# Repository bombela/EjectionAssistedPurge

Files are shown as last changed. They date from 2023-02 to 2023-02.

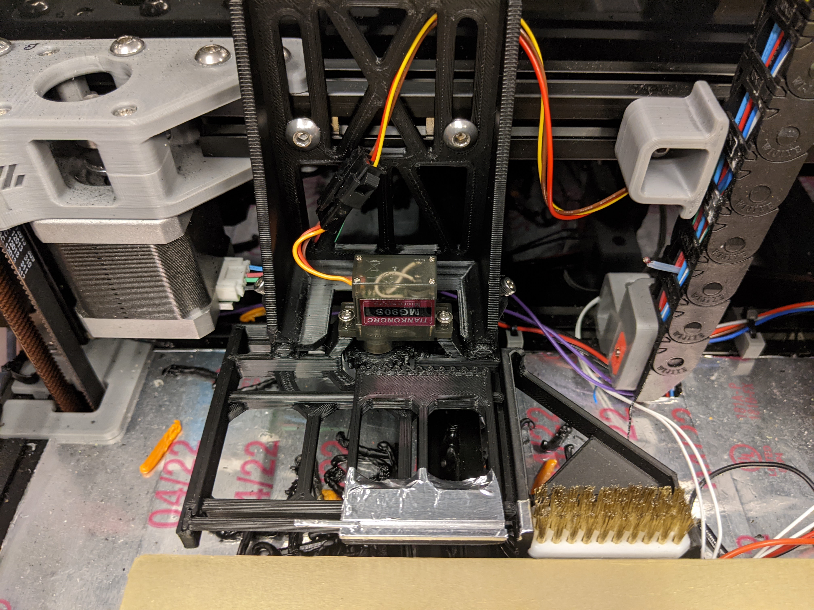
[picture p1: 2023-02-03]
doc/installed_closeup.jpg

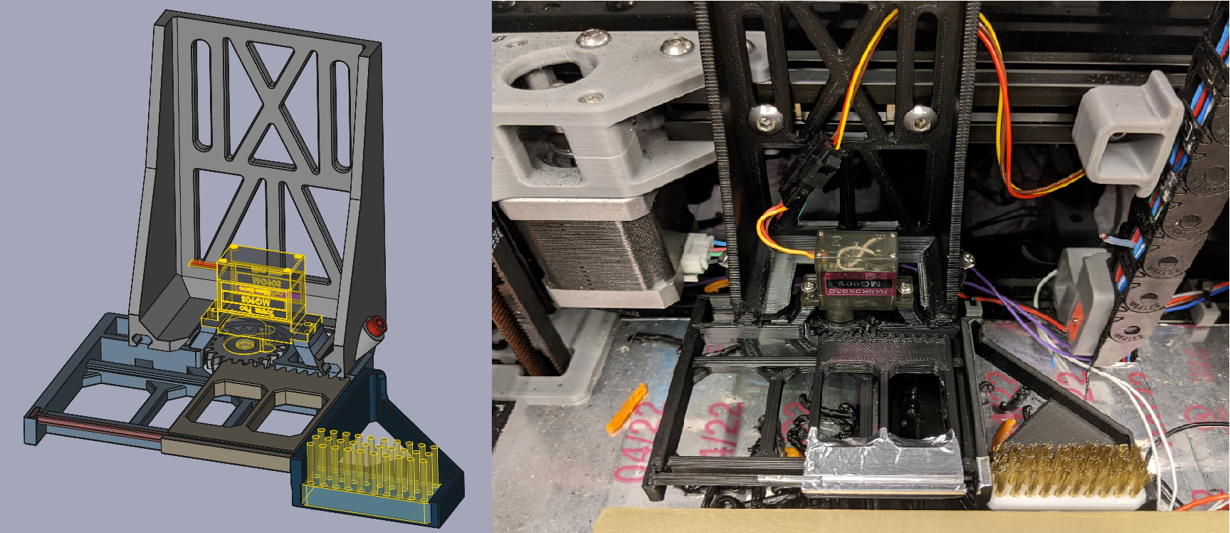
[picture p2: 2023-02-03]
doc/overview.png

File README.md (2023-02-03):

# EjectionAssistedPurge (EAP)

https://user-images.githubusercontent.com/216204/216499002-51c40538-1833-44a0-8337-d1b87039a244.mp4

Designed for the Voron 2.4r2. Should work on Voron Trident. Feel free modify it for other printers.
There are macros for Klipper to brush, purge, and integrate with the slicer toolchange.

The EAP can purge from 15mm³ to 185mm³. For reference, the default purge amount in PrusaSlicer and SuperSlicer is 140mm³.

It is especially useful with an automatic filament changer, like the [ERCF](https://github.com/EtteGit/EnragedRabbitProject).

# Overview

overview

The EAP mounts on the gantry of a Voron 2.4 (or the frame for a Trident). Therefore it is always at the same Z height as the nozzle.
It is adjustable in Z and Y. Purging is done into a groove with a dovetail shape designed to hold the hot plastic, and resist curl up.
The groove is covered with adhesive metallic foil to quickly cool the surface of the extrusion and prevent adhesion.

The plastic should be left to cool from 15s (ABS) to 30s (95A TPU) before ejection.
In practice, automatic filament changes takes about 30s, so even printing a single dot between swaps gives it enough time to cool.

The Grove is 1mm from the edge of the tray, and 2mm wide. This means that the tray can be as close as possible to the bed,
and only a couple milimeters past the back end of the bed. With the stock Voron 2.4r2 nothing has to be adjusted.
It is similar to reaching out to the nozzle endstop.

An ubiquitous RC Servo MG90S is used to actuate the tray against a piston and eject the solidifed plastic. There is no provision
to catch the plastic turds. They accumulate at the bottom of the printer, and this can be cleaned up from time to time.

It has been tested succesfully with ABS, PLA, PETG and 95A TPU.

# Printing, BOM, and assembly

parts laid out for printing

All the [STL/STEP files](/stl) files are oriented for printing. The screenshot above shows all the parts spread out.

The design is optimized for ABS and accounts for shrinkage. I slice with arachnea, 0.2mm layer height, 0.4mm nozzle, 4 perimeters, 5 layers bottom/top, and 15% gyroid infill. Standard Voron recommended settings should also work fine.

## Bill of material

 - 2× (M5x8 + M5 tnut) for mounting the bracket on the gantry (and finely adjust in Z).
 - 2× M3x8 to lock the frame in  Y adjustment.
 - MG90S or similar RC servo 180° and the screws that come with it.
 - Aluminum adhesive tape: ~10µm thick, 20 to 40mm wide.
 - A brass brush, you know, the one we all use.
 
And for RC servo connection on the Octopus board:
 - 3×24 awg 150cm long
 - JST-XH 2pins male connector
 - JST-XH 3pins male connector
 - Optional, some wire-to-wire connector near the servo for conveniance.

## Assembly instructions

### Adhesive aluminum tape

The difficult part is the aluminum adhesive foil on the tray. Refer to the pictures for where to place the tape.

A trick is to fold it, insert it in the groove. Then gently spread it out with the shaft
of a thin screwdriver used in its whole length.
It is important for the foil to follow the contour of the grove tightly. Otherwise it will rip when the piston moves through.
Manually insert the piston and test. Redo the work if necessary, it took me 5 tries the first time.

You can extend the aluminum foil over the tray up to the rack teeth with another piece if necessary.
The large the surface area, the better the cooling.

Add a piece of adhesive aluminum tape at the tip of the piston. No need to cover the whole thing, nor the sides.
Just enough to cover the tip and prevent plastic from sticking. Finally, add one more small piece on the edge if the brush holder.
ABS tends to slide off the groove very easily and follow the nozzle. It could stick on the edge of the brush holder.

### Printed parts

Everything slides with dovetails. Install the tray first. The piston next. Slide the brush holder after that.
Insert the brush at the end, its easy to prick fingers otherwise.

Mount the pinion gear on the servo and the screw. Screw it quite tight. There is up to 1kg of force on the gear.
Then gently turn the gear into counter-clockwise (ie: as if unscrewing) until you reach the end of travel. Don't break the poor servo!

This way the gear is set for when the tray is all the way opened to the left. Place the tray all the way to the left,
the the servo. It is ok for the tray to not touch the frame when the gear engages. There is some margin on both sides.
Use the two M2 self-tapping screws that come with the servo to mount it on the frame.

Finally slide the frame into the bracket. Add the two M3 screws. Mount the bracket on the gantry. I choose to install
mine on the left side. And my [Klicky probe](https://github.com/jlas1/Klicky-Probe) on the right. I suppose you could
mirror the parts before printing. The Klipper macros are agnostic of the direction.

An easy way to install flush to the bed in Z and Y is to instruct the printer to move the toolhead to the far front and lower the nozzle on the bed.
Then the bracket can be mounted to the granty with the M5 screws and T-nut.
It is easy to adjust the Y and Z such that the top of the tray is flush with the top of the and side of the bed.
Do leave a minimum of 0.5mm from the edge of the bed. There a tiny bit of margin here, the nozzle doesn't have to be perfectly in the middle of the
grove, nor perfectly flush with the top surface of the tray.

The frame is locked in Y with the two M3 screws. No need to over-tighten there. It's threaded into plastic. 

The brush holder can be adjusted in Y independently by sliding the dovetail. For example if you want a larger gap from the bed and the tray,
you can move the brush forward a bit to get a better scrubbing of the nozzle.

### Electronics

You do need one available digital pin to control the servo. And a 5V supply.
With the Octopus board (stock Voron 2.4r2), I used PG12 on the DIAG4, and the fixed FAN7 output set for 5V.
This way, the wiring is tidy. You will need to crimp the JST connectors (listed in the BOM above).



Thread the wire through the Z drag chain. Follow the path of the nearest A/B motor wiring.

# Klipper macros

Include the `eap.cfg` in your Klipper configuration (most likely in `printer.cfg`).
Carefuly adjust the configuration variables at the top of the file.
Manually control your toolhead with Klipper to find out of the exact XY positions of the groove and the brush.

The macros and their parameters are documented in detail the file.

Ejection is done before purging. Maximizing the cooling time between purges.
This does wastes 2s before purging.
Klipper would need to be modified to support asyncronous actuation of the ejection.
I do not swap filament often, so for now this has not bothered me.

Here a summary of the macros:

|Macro|Description|
|-|-|
|BRUSH|Brush the nozzle. Useful in PRINT_START, PRINT_END, homing and Quand Gantry Leveling and so on.|
|PURGE|Eject, then purge and plow through the brush.|
|PURGE_HOME|Place the toolhead near the groove then eject. Used before a toolchange, see example of use in PrusaSlicer below.|
|PURGE_EJECT|Trigger an ejection. Useful for testing.|

## Use in PrusaSlicer

Here is an example of use in prusaslicer tool change gcode. When the wipe tower is turned off,
the Ejection Assisted Purge is used.

```
{if has_wipe_tower}
  T{next_extruder} ; ERCF swap { filament_preset[current_extruder] }
{else}
  PURGE_HOME ZHOP=0.2 ZCHECK=0
  T{next_extruder} ; ERCF swap { filament_preset[current_extruder] }
  PURGE VOL=150 RET=0.5 RETSPEED=35 EJECT=0 BRUSH_CLEAR=0 ZCHECK=0
{endif}
```

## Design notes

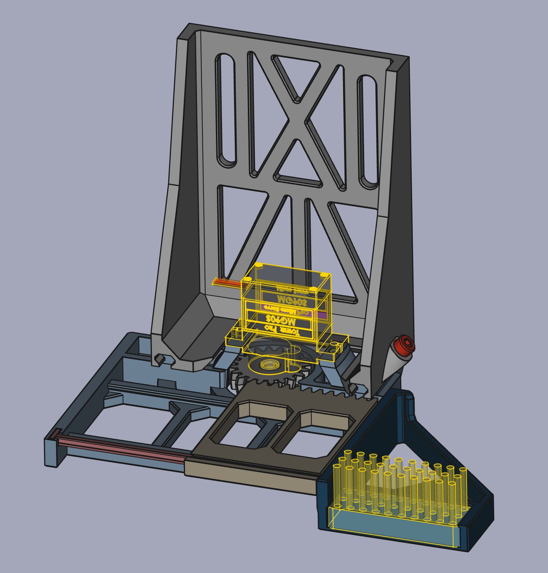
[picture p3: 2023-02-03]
doc/cad.jpg

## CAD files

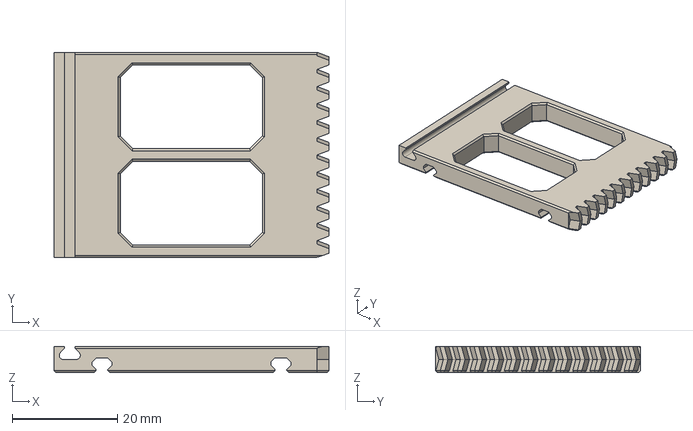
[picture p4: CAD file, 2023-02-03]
stl/eap_tray.step
52.2 x 39.0 x 5.00 mm

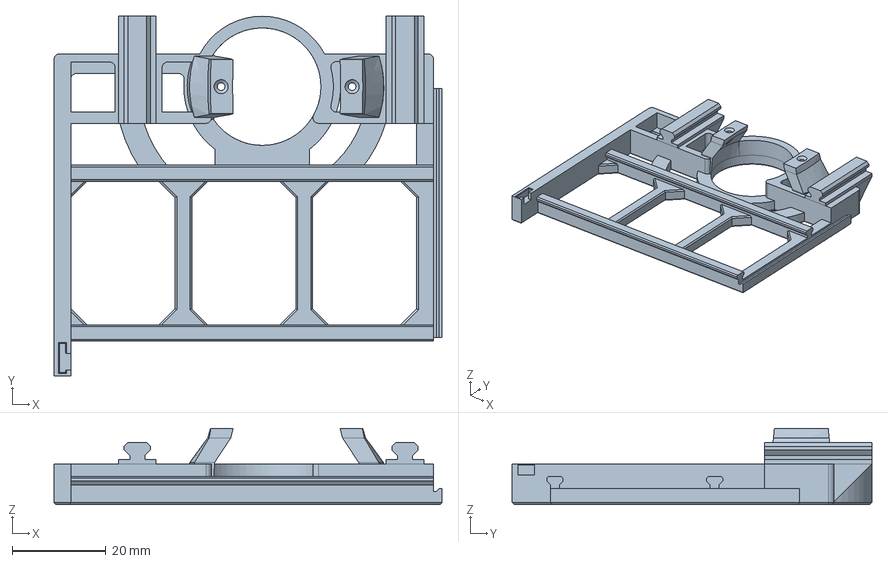
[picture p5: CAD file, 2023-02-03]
stl/eap_frame.step
82.6 x 76.5 x 16.2 mm

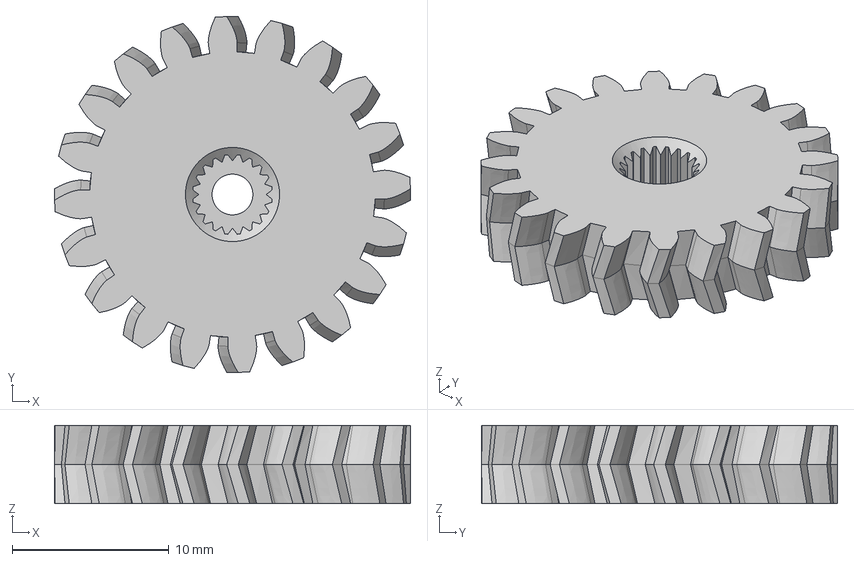
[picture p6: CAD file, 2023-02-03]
stl/eap_pinion.step
22.7 x 22.7 x 5.00 mm

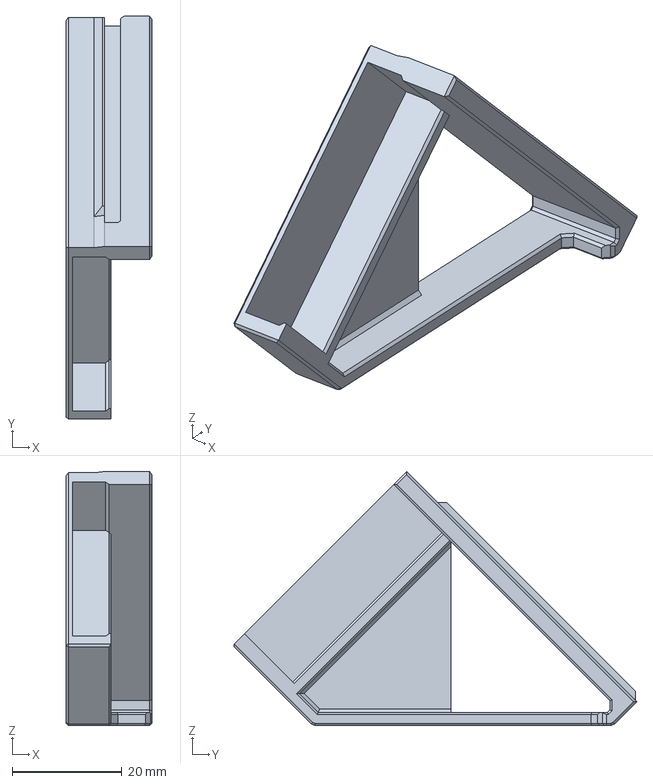
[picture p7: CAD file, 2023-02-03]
stl/eap_brush_holder.step
15.6 x 73.2 x 46.2 mm

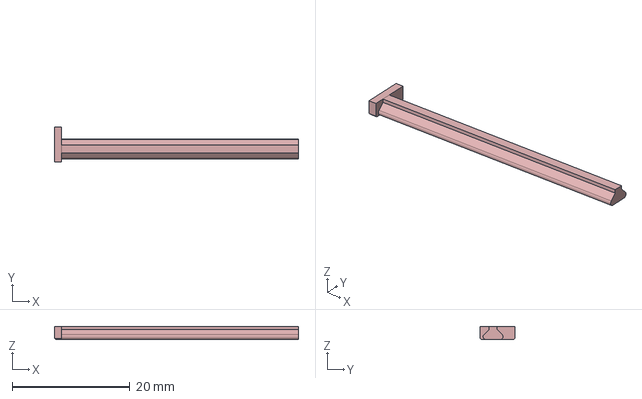
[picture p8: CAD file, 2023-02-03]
stl/eap_piston.step
41.4 x 6.00 x 2.20 mm

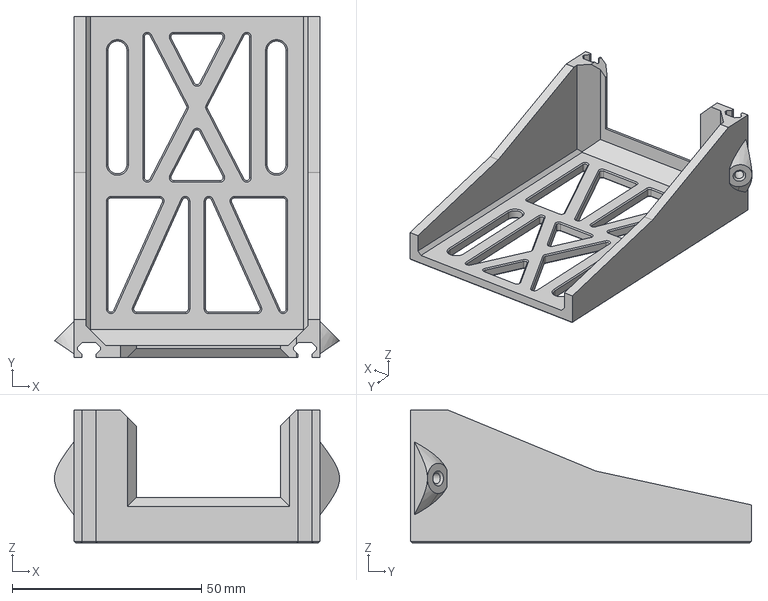
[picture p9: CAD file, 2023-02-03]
stl/eap_bracket.step
75.2 x 90.0 x 35.0 mm

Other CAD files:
stl/eap_bracket.stl
stl/eap_brush_holder.stl
stl/eap_frame.stl
stl/eap_pinion.stl
stl/eap_piston.stl
stl/eap_tray.stl

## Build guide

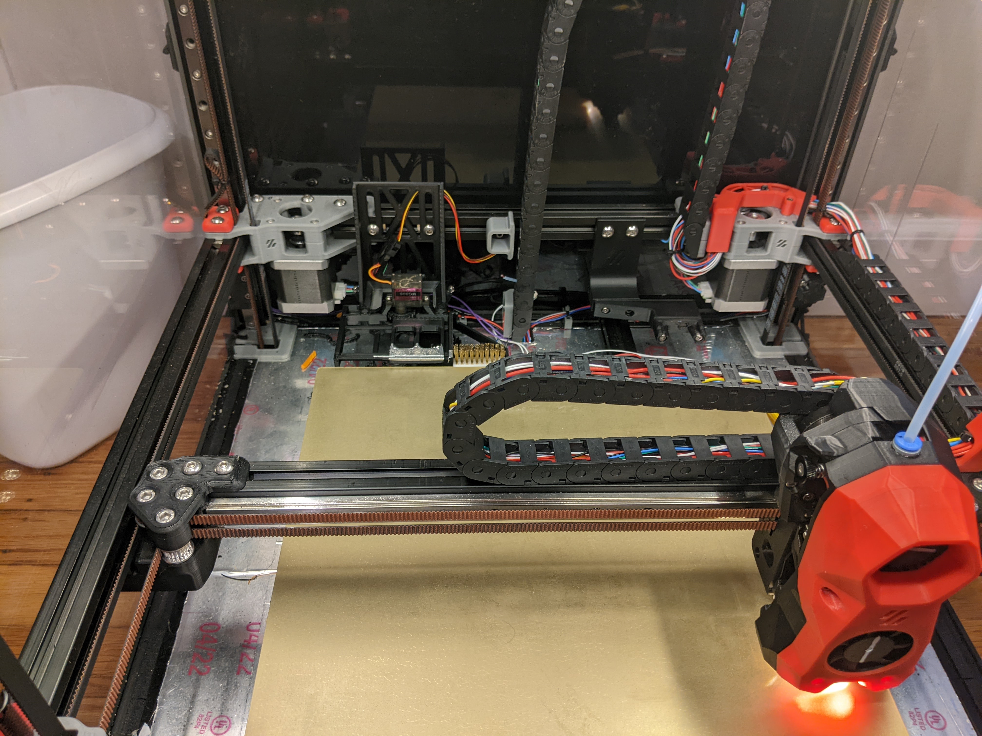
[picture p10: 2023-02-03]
doc/installed_overview.jpg

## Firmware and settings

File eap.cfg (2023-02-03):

# vim: tabstop=4 shiftwidth=4 expandtab

# Ejection Assisted Purge (EAP).
# Macros for Klipper.
# BRUSH
# PURGE
# PURGE_HOME
# PURGE_EJECT

[servo eap_servo]
pin: PG12
maximum_servo_angle: 180
minimum_pulse_width: 0.00050
maximum_pulse_width: 0.00250

[gcode_macro _PURGE_CFG]
# A central place for the configuration of all the macros in this file.
gcode:
#### Brushing.
# X,Y start position. A few mm past the right side of the brush.
variable_brush_start: 130, 305
# X stroke relative to the start. A few mm past the left of the brush.
variable_brush_stroke: -40
# X distance relative to the start position to clear away from the brush.
variable_brush_clear: 30
# Brushing speed in mm/s.
variable_brush_speed: 400
# How many times to brush.
variable_brush_count: 3
#
#### Purging.
# X, Y start position of the purging groove. A bit on right side of the end of
# the piston.
variable_groove_start: 50, 305
# Position relative to the start of the grove where to wait for cooling and
# ejection.
variable_cooling_pos: 15, -10
# Minimum cooling time in seconds. If less than the cooling time has elapsed,
# the next purge will wait for the end of the cooling period with the cooling
# fan atop.
variable_cooling_period: 15
# Default purging amount in mm³.
variable_volume: 140
# Default purging flow rate in mm³/s. Depends on the hotend, extruder, and
# viscocity of the plastic.
variable_flowrate: 20
# After a purge at a high flow rate, some pressure is left in the nozzle.
# A bit of retraction can even it out. Volume in mm³.
variable_retraction: 5.
# Retraction speed in mm/s.
variable_retraction_speed: 35
# Length of the groove relative (X) to the start.
variable_groove_len: 35
# Filament crosssection area in mm².
variable_fil_csa: 2.405 # 1.75mm filament.
# Groove crosssection area in mm².
variable_groove_csa: 5.3
#
#### Ejection.
# How long it takes to actuate the servo all the way.
# A MG90S servo is usually rated at 1.8ms/deg at 4.8V.
# Add some margin. For example 1.8ms*180 = 324ms -> 400ms.
variable_servo_dwell: 400
# How many actuations. Sometimes the pellet get stuck or missplaced, and
# another ejection fixes it.
variable_ejection_count: 2
#
#### General.
# Z limit. Below this height, refuses to do anything as a safety measure.
# The check can be turned off by passing ZCHECK=0 to the macros.
variable_z_min: 5
# Travel move speed in mm/s.
variable_travel_speed: 500

[gcode_macro BRUSH]
# This macro doesn't move in Z, only X and Y.
# Parameters:
#   CLEAR=1
#   ZHOP=-1
#   ZCHECK=1
gcode:
    # Clear away from the BRUSH at the end. Can be skipped to save a move.
    {% set clear = params.CLEAR|default(1)|int %}
    # Z hop if positive value.
    {% set zhop = params.ZHOP|default(-1)|float %}
    # Raise an error if z < z_min.
    {% set zcheck = params.ZCHECK|default(1)|int %}

    {% set cfg = printer['gcode_macro _PURGE_CFG'] %}
    {% set tspeed = cfg.travel_speed * 60 %}
    {% set wspeed = cfg.brush_speed * 60 %}
    {% set sx = cfg.brush_start[0] %}
    {% set sy = cfg.brush_start[1] %}

    {% if "xyz" not in printer.toolhead.homed_axes %}
        { action_raise_error("Not homed") }
    {% elif zcheck and printer.toolhead.position.z < cfg.z_min %}
        { action_raise_error("Z too low") }
    {% else %}
        SAVE_GCODE_STATE NAME=BRUSH
        {% if zhop >= 0.0 %}
            G91 # relative
            G0 Z{zhop} F{tspeed}
        {% endif %}
        G90 # absolute
        G0 X{sx} Y{sy} F{tspeed}
        {% for _ in range(0, cfg.brush_count) %}
            G0 X{sx + cfg.brush_stroke} F{wspeed}
            G0 X{sx} F{wspeed}
        {% endfor %}
        {% if clear == 1 %}
            G0 X{sx + cfg.brush_clear} F{tspeed}
        {% endif %}
        {% if zhop >= 0.0 %}
            G91 # relative
            G0 Z{-zhop} F{tspeed}
        {% endif %}
        RESTORE_GCODE_STATE NAME=BRUSH
    {% endif %}

[gcode_macro PURGE]
# Eject the previous purge, then purge and plow through the brush.
# Parameters:
#   VOL=cfg.volume
#   FLOW=cfg.flowrate
#   RET=cfg.retraction
#   RETSPEED=cfg.retraction_speed
#   BRUSH_CLEAR=1
#   EJECT=1
#   ZHOP=-1
#   ZCHECK=1
#
# Maximum purge volume: abs(groove_len) * groove_csa.
# Example: 35mm * 5.3mm³ == 185mm³
variable_last_purge: 0.0
gcode:
    {% set cfg = printer['gcode_macro _PURGE_CFG'] %}

    # The amount to purge in mm³.
    {% set vol = params.VOL|default(cfg.volume)|float %}
    # The purging flow rate in mm³/s.
    {% set flow = params.FLOW|default(cfg.flowrate)|float %}
    # The retraction amount in mm³.
    {% set retvol = params.RET|default(cfg.retraction)|float %}
    # The retraction in mm/s.
    {% set retspeed = params.RETSPEED|default(cfg.retraction_speed)|float %}

    # Clear away from the BRUSH at the end. Can be skipped to save a move.
    {% set brush_clear = params.BRUSH_CLEAR|default(1)|int %}
    # Call PURGE_HOME before purging.
    {% set eject  = params.EJECT|default(1)|int %}
    # Z hop if positive value.
    {% set zhop = params.ZHOP|default(-1)|float %}
    # Raise an error if z < z_min.
    {% set zcheck = params.ZCHECK|default(1)|int %}

    {% set tspeed = cfg.travel_speed * 60 %}
    {% set max_vol = (cfg.groove_len|abs * cfg.groove_csa) %}
    {% set sx = cfg.groove_start[0] %}
    {% set sy = cfg.groove_start[1] %}
    {% set initial_fan_speed = printer.fan.speed / printer.configfile.settings.fan.max_power %}

    {% if "xyz" not in printer.toolhead.homed_axes %}
        { action_raise_error("Not homed") }
    {% elif zcheck and printer.toolhead.position.z < cfg.z_min %}
        { action_raise_error("Z too low") }
    {% elif vol > max_vol %}
        { action_raise_error("Purge volume %.3fmm\u00B3 greater than maximum %.3fmm\u00B3" % (vol, max_vol)) }
    {% else %}
        SAVE_GCODE_STATE NAME=PURGE
        {% if zhop >= 0.0 %}
            G91 # relative
            G0 Z{zhop} F{tspeed}
        {% endif %}
        G90 # Absolute positioning.
        {% if eject %}
            PURGE_HOME ZCHECK={zcheck}
        {% else %}
            G0 X{sx} Y{sy} F{tspeed}
        {% endif %}
        M106 S255
        M83 # relative extruder
        # purge
        {% set dist = vol / cfg.groove_csa %}
        {% set feed = flow / cfg.groove_csa %}
        {% set fil = vol / cfg.fil_csa %}
        # Sometimes, randomly it almost seems, klipper decides it really wants ascii in some processing happening in action_respond_info. Maybe some logging going wrong?
        #{ action_respond_info("purge: vol=%.3fmm\u00B3 flow=%.3fmm\u00B3/s dist=%.3fmm fil=%.3fmm rate=%.3fmm/s" % (vol, flow, dist, fil, feed)) }
        { action_respond_info("purge: vol=%.3fmm3 flow=%.3fmm3/s dist=%.3fmm fil=%.3fmm rate=%.3fmm/s" % (vol, flow, dist, fil, feed)) }
        G1 X{sx + dist} E{fil} F{feed * 60}
        # retraction
        {% set ret_fil = retvol / cfg.fil_csa %}
        G1 E-{ret_fil} F{retspeed * 60}
        # brush
        G0 X{cfg.brush_start[0]} Y{cfg.brush_start[1]} F{cfg.brush_speed * 60}
        M106 S{initial_fan_speed * 255|int}
        {% if brush_clear == 1 %}
            G0 X{cfg.brush_start[0] + cfg.brush_clear} F{tspeed}
        {% endif %}
        {% if zhop >= 0.0 %}
            G91 # relative
            G0 Z-{zhop} F{tspeed}
        {% endif %}
        RESTORE_GCODE_STATE NAME=PURGE
    {% endif %}
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
